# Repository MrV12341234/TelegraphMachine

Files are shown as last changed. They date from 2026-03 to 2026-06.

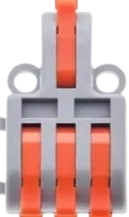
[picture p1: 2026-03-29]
imagesForSchematic/1in3out-removebg-preview.png

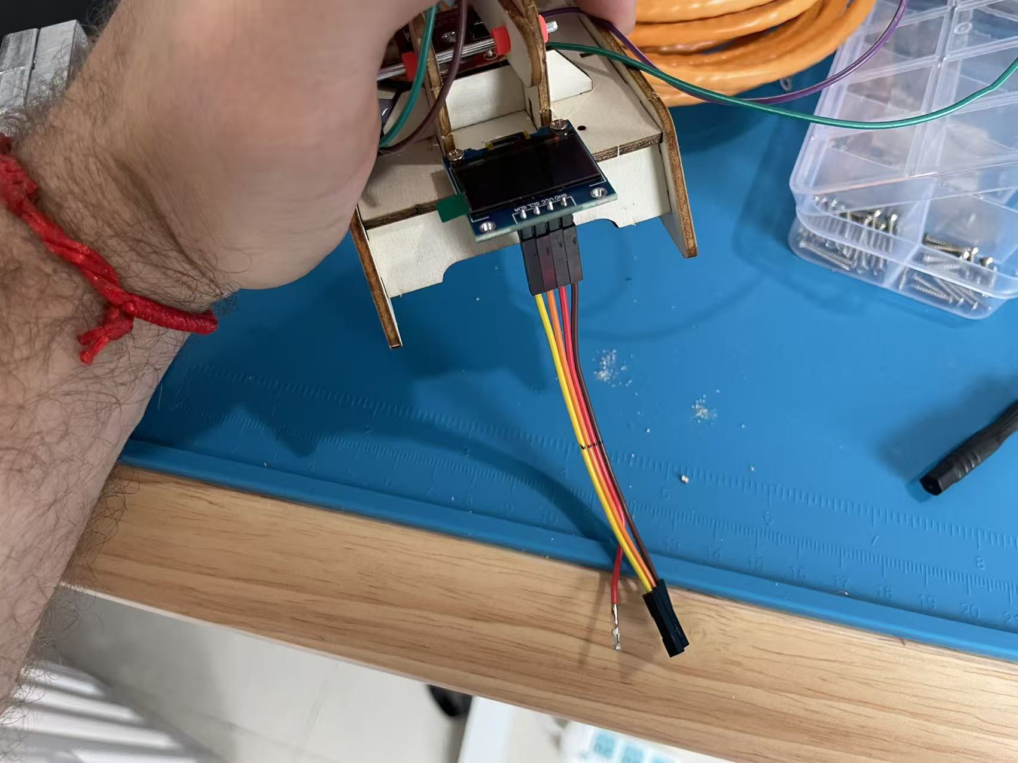
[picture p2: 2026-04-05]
imagesForSchematic/Instruction Images/ScreenWiring.jpg

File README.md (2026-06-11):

This Machine uses Telegraph DIY kits, adding an Arduino Nano and
OLED screen to send and receive telegrams.

Operation:
Either side can begin sending a message. Once one side begins, the other now must wait.
When the sender finishes (waits 7 seconds), the message will send.
The system pauses until the receiver presses their button. Then everything is reset.

Wiring:

OLED:
GND → GND
VCC → 5v board power
SDA → A4
SCK/SCL → A5

Button: one side ground, other side goes to  D2
Buzzer: One side ground, another side goes to D6

Board A D11 → Board B D10
Board B D11 → Board A D10
Board A GND → Board B GND
Board A 5V → Board B 5V
(this connection eliminates the need to power the second nano with a power source)

end of document..

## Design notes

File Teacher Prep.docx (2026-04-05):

Teacher Prep – Telegraph Machines

Materials to buy:

https://docs.google.com/spreadsheets/d/10zAsUNHxBq-jBxFfgv1lAB1i47ZYRMRfzh0iq-26aYY/edit?gid=0#gid=0

Silicon mat for each team (to pick up project and move it each day)

Long wiring from each station (4 wires each run)

2 Nano’s (one per station)

2 OLED (128x64)

2 bread boards

2 DIY telegraph kits (will not use as instructed)

Breadboard pins (both male to male and female to female

Hot glue gun

Boxes (about 10cm x10cmx5cm). No problem if its bigger.

MrV to prep for each group:

- Solder wires to button board (see photo). Use the edge colors of each groups long female to female wire jumper set. Remove the black plastic from green ground wire. Cut off ant and black/red wires from the board. UPDATE: TEACHER NEEDS TO REMOVE 2ND BUTTON AND BLUE A DIFFERENT BUTTON ON THE BOARD.

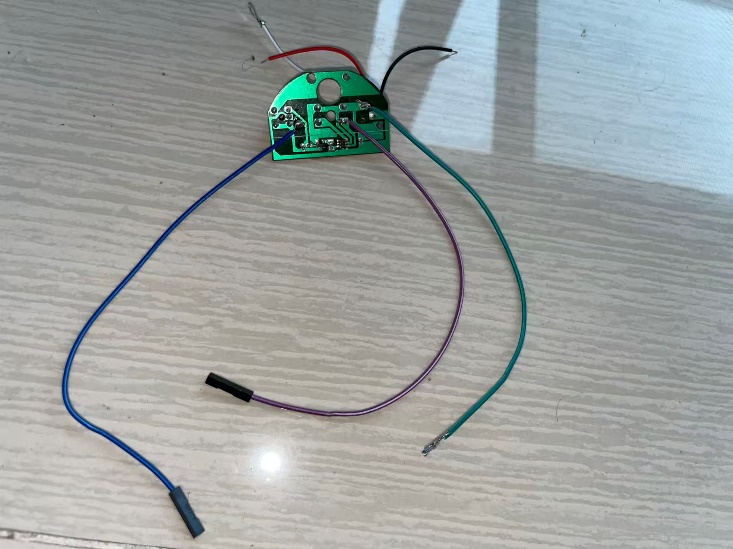
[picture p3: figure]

- Solder the ends of the ground wires for the buzzer ground and the button grounds so they more easily can go into the wire connectors
- Pre-drill box holes:
  - in top of wood box (number 20 on the step bit)
  - front (ethernet cable, 10 on step bit)
  - Side of ONE Box per group (usb, 14 on step bit)
- Create wire harness for OLED screens. Take black platic end off the VCC (5v) wire to put into the connector

Introducing the project:

Explain what a nano is (how each pin either accepts input or put output.

Explain how a machine reads code

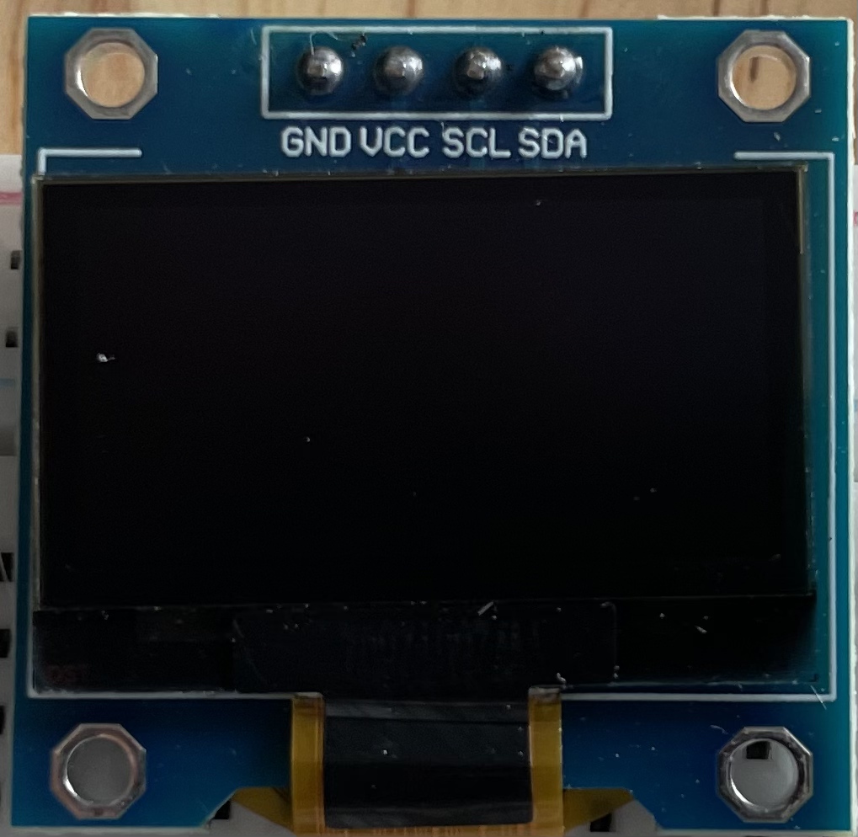
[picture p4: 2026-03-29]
imagesForSchematic/OLED.jpg

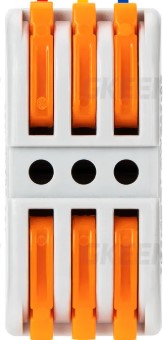
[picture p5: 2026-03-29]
imagesForSchematic/SchematicImages/3in3out.jpg

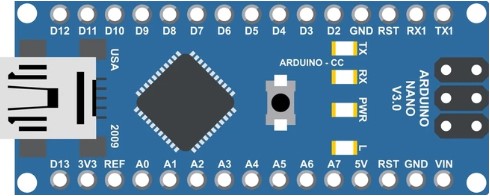
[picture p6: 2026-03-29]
imagesForSchematic/NanoCartoon.jpg

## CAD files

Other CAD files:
WiringSchematic.dwg

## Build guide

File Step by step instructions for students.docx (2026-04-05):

Step by step instructions for students

1. You will first setup the two 11cmX11cm boxes. This telegraph system has a sender and receiver box. The boxes are very similar but have slight differences in the wiring and the sender box has an additional hole for the power.
2. Drill 2cm hole in top of box

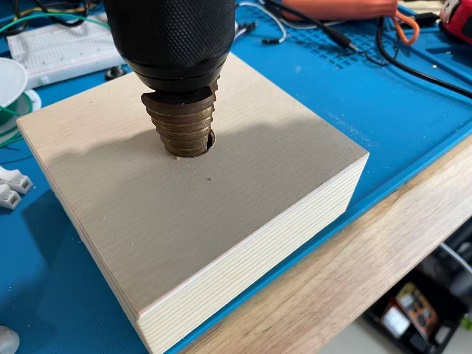
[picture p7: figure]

3. Drill 14mm hole in front of box. The “receiver” box will have only these two holes. For the “sender” box you need to drill a second 14mm hole in one of your two boxes, one box needs a usb cable).
4. Unpackage and remove the items from the Telegraph kit. These are the only parts we will use from this kit:

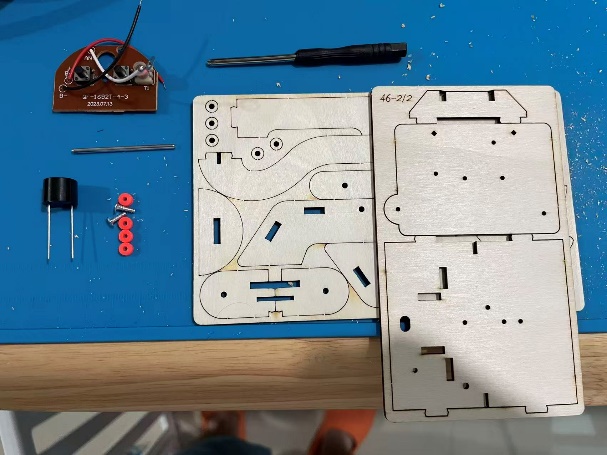
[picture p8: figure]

5. Ensure the brown button board has the wires added for this project (teacher will have previously done this).

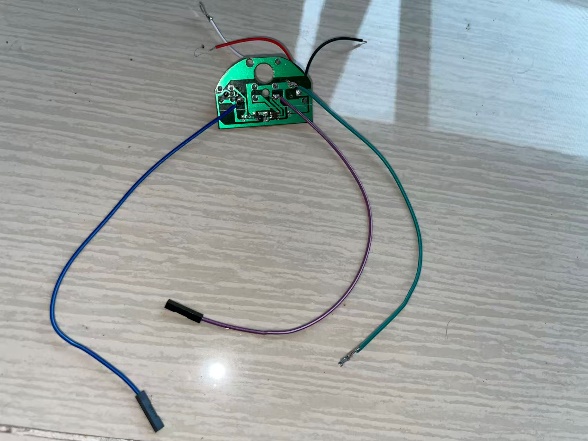
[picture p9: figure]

6. Assemble the telegraph kit with the parts shown in step three:

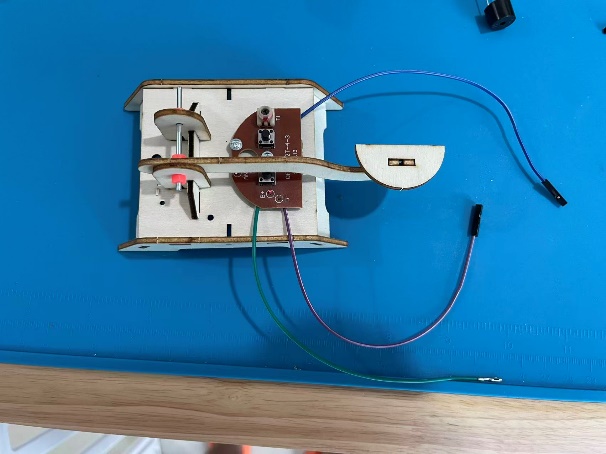
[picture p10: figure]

7. Take the black buzzer. Attach a long BROWN wire to the plus (+) terminal. Attach a GREEN wire to the other side. Remove the black plastic end from the other end of the green wire

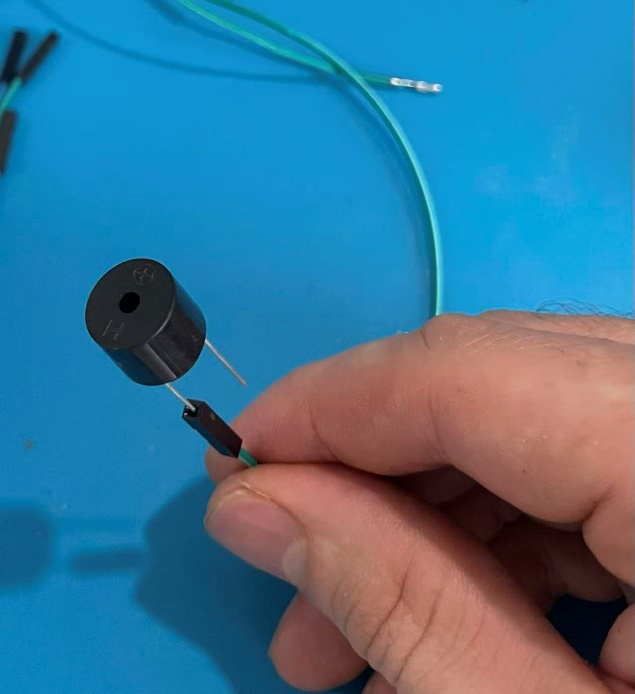
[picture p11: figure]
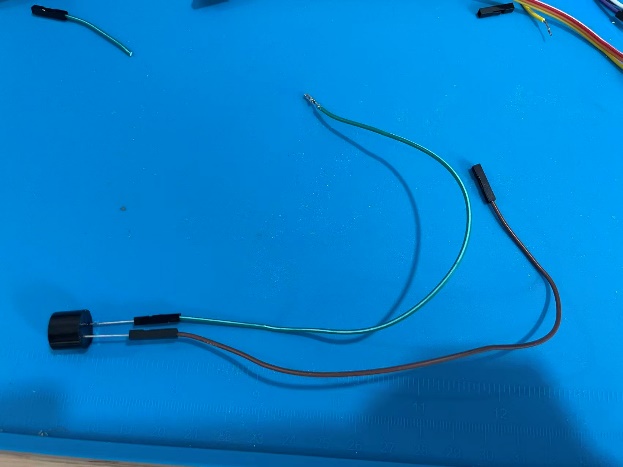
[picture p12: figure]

8. Apply hot glue to both the green and brown connection (see photo below). Ensure no glue is going between the silver posts. Then mount the buzzer somewhere on the telegraph machine using hot glue.

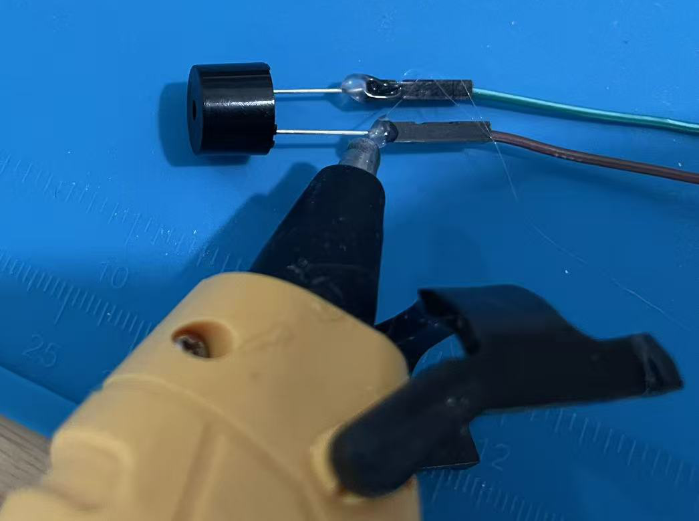
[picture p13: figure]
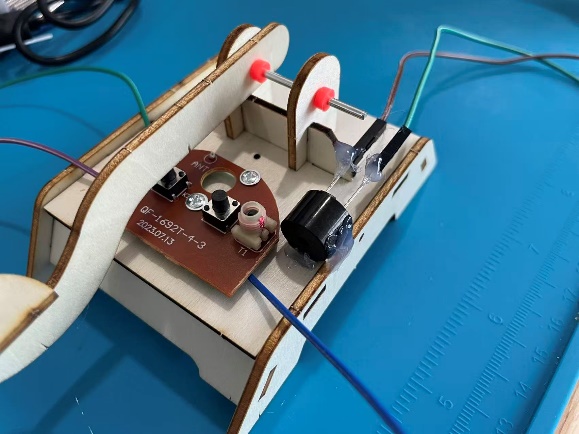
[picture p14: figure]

9. Use a pen to mark the holes of the screen. Drill one hole with a 1.5mm drill bit to drill the holes. Use 2 of the wooden spaces provided in the kit as a spacer between the screen and the base. Mount the screen with one hole then drill the second hole through the hole of the screen. Use two screws to attach (you need different screws than came in the kit).

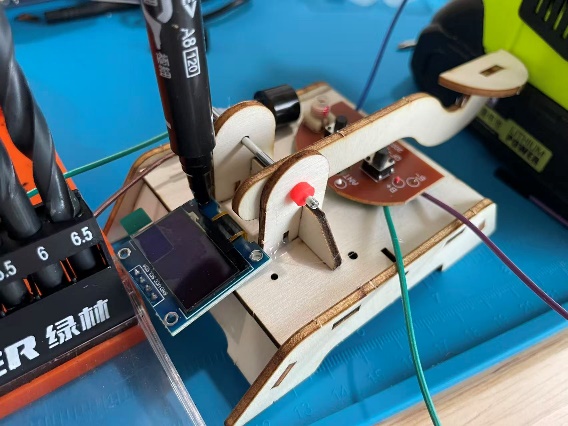
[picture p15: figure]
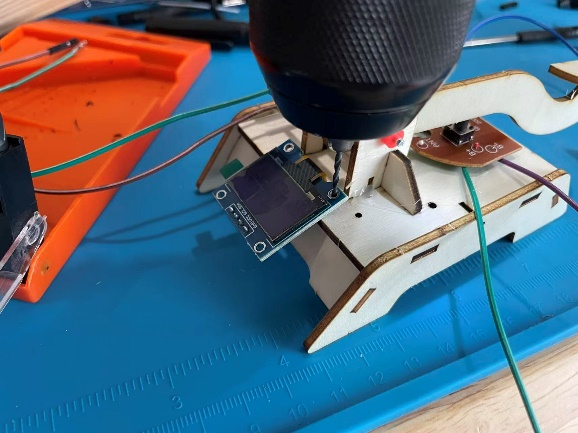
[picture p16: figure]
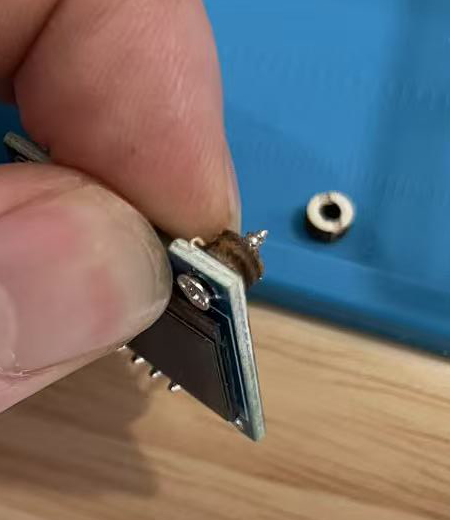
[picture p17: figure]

Alternatively, you can use a hole on the kit and mount the screen using the bottom left hole. The screen will be a little sideways, but the install is much easier:

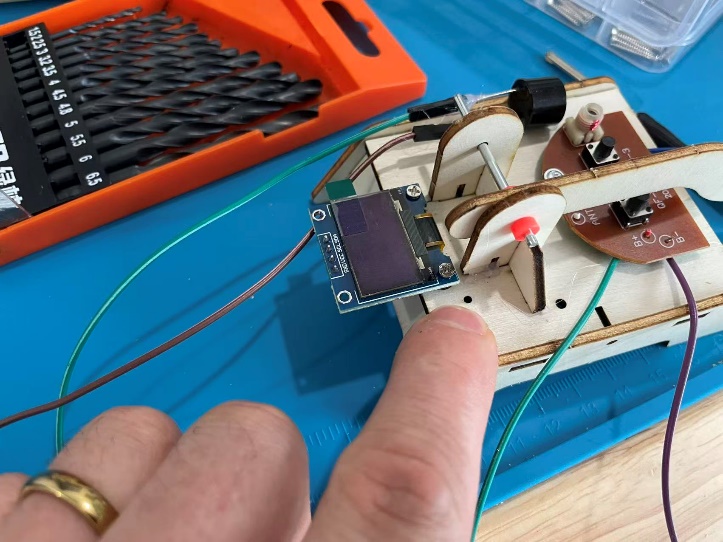
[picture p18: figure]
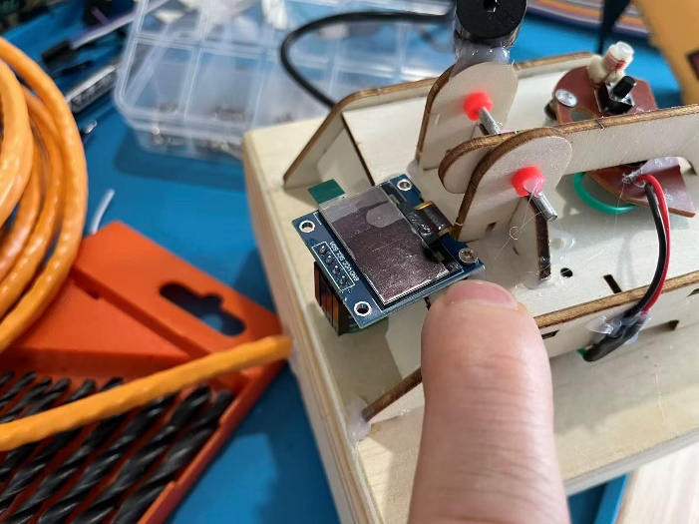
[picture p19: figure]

10. Take these four wires from your short Female-to-female wire set. Ensure the colors are like this: GND → Brown (GN )

VCC → Red (5v board power )

SCL → Orange (A5)

SDA → Yellow (A4)

Remove the black plastic end from the Red wire

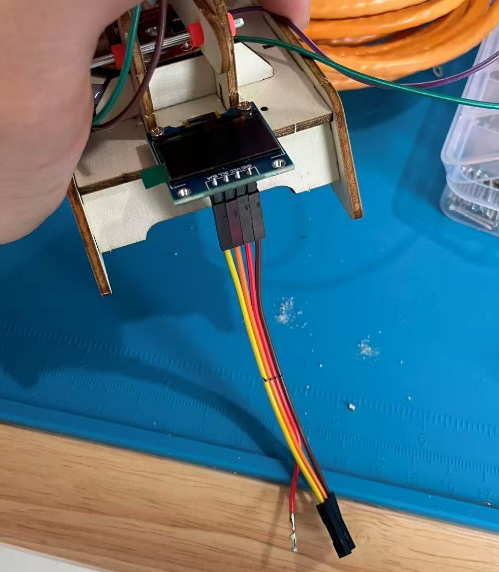
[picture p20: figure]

11. Now that the Telegraph button half is finished, insert all the wires into the large hole of your box. See the below photos to see how to route each device wires into the hole. ENSURE THE SCREEN IS FACING THE “FRONT” WHERE THE SIDE HOLE IS LOCATED. Add two small hot glue welds to secure the telegraphy machine to the box (when the project is complete we will put more glue here).

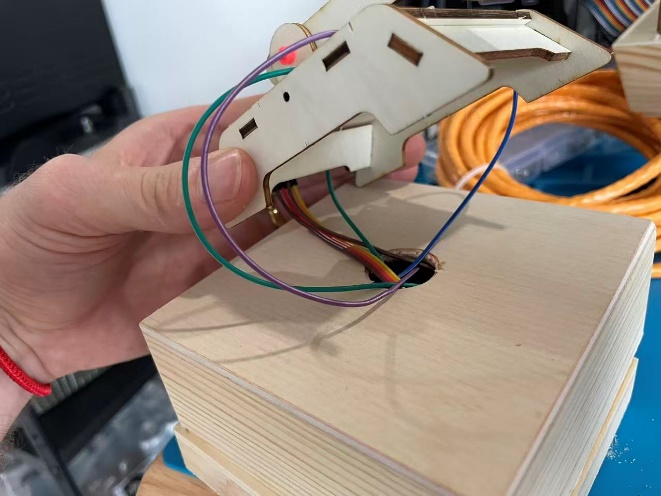
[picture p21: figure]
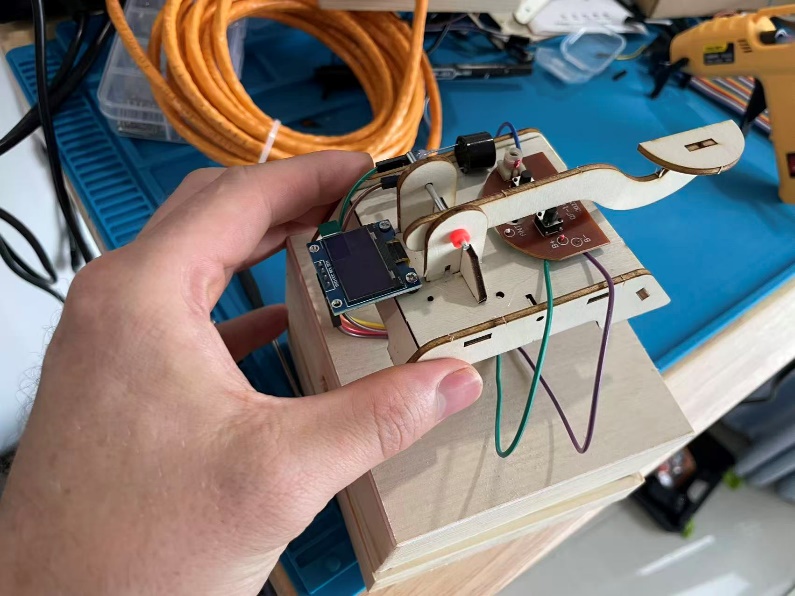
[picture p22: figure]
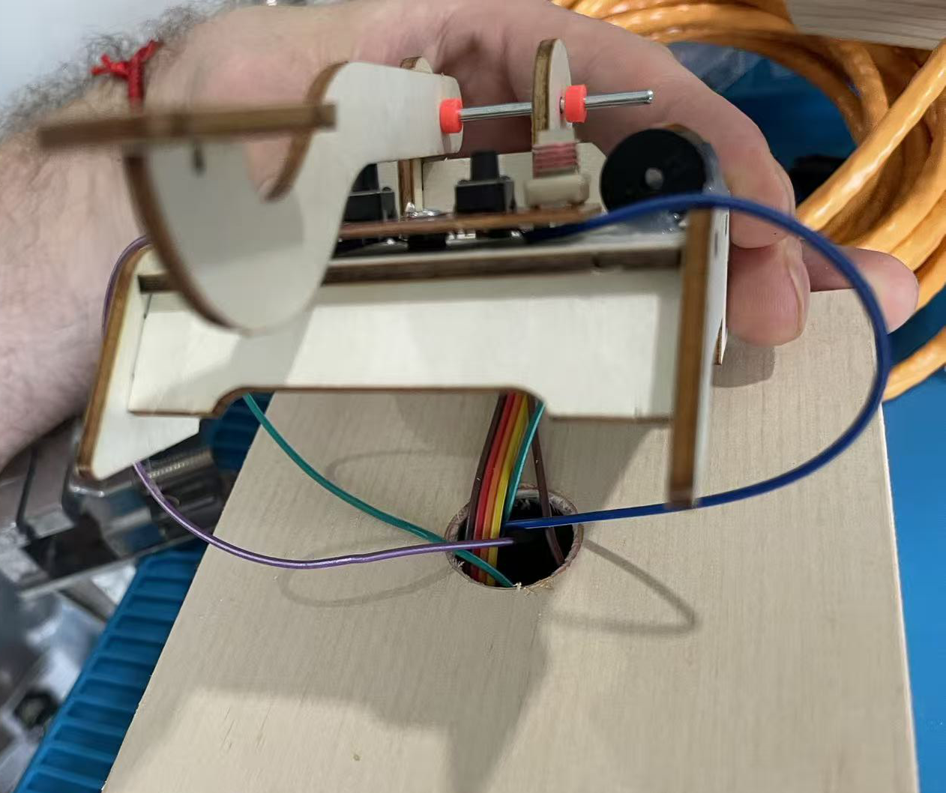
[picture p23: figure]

12. Prepare (splice) the ethernet cable so its ready to be connected. Optionally, you can install a female-to-female RJ45 (Ethernet) connector to the box to avoid a permeant connection between the two boxes. See photos below.  To prepare the ethernet cable, strip back the plastic coating about 1.5cm from the ends of each of the 8 wires inside.

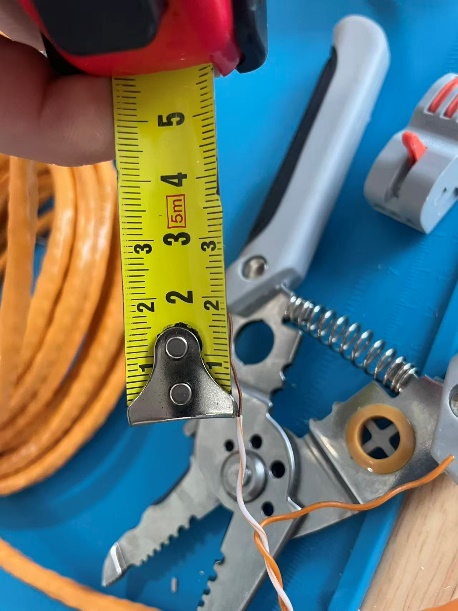
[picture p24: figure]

After stripping all the ends, twist together the bare ends of each color. Green to green, orange to orange, brown to brown, and blue to blue:

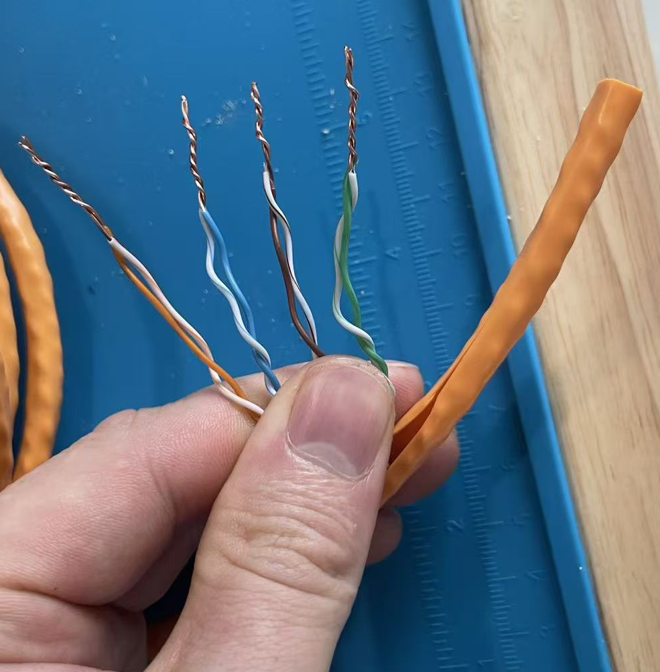
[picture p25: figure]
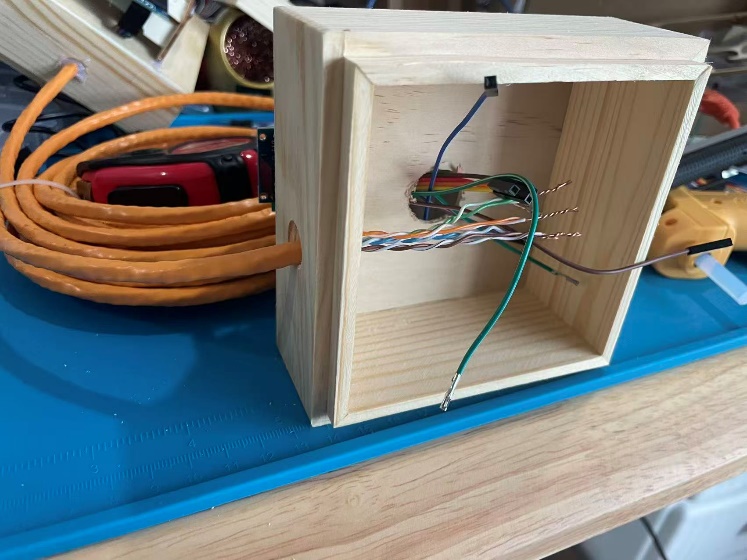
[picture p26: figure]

These are the optional RJ45 to Rj45 connectors you can use for a quick disconnect and making the boxes more portable:

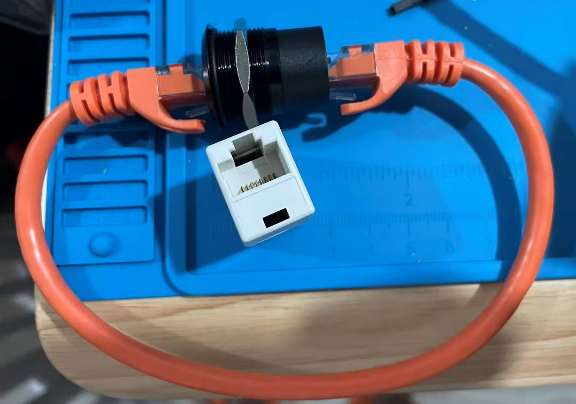
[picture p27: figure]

13. Take the black plastic off a red, green, blue, and orange wire from your short female-to-female wires:

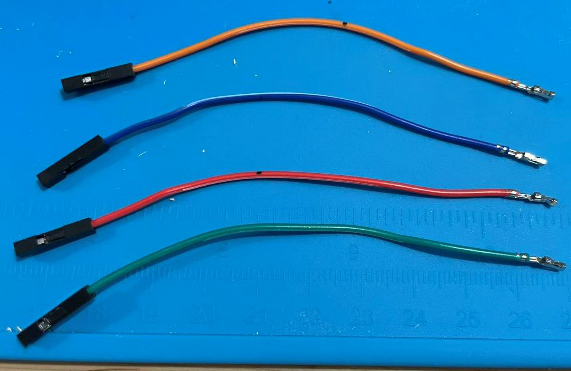
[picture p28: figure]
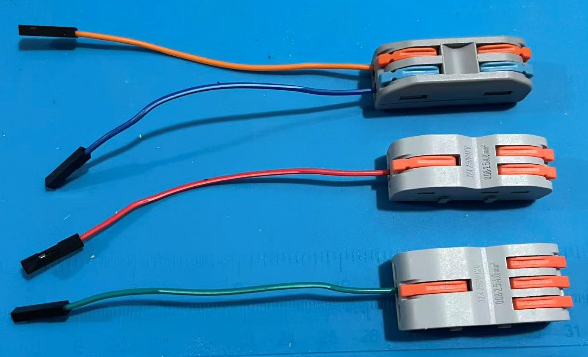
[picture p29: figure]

14. Follow the wiring schematic to hook everything up. IMPORTANT: The wiring diagram is for the sender box. The receiver box will have D10 and D11 switched. On the receiver box, D10 should have the orange wire an D11 the blue wire. Otherwise, all the grounds go into the 3-to-1 connector with the single side going to the computer. The screen goes to a 2-to-1 connector. The other side of the 2-to-1 connector goes to the opposite box same connector.

Button: one side ground, other side goes to D2

Buzzer: One side ground, another side goes to D6

15. When finished and confirmed the system is working, put a small amount of hot glue on each connection to the computer.

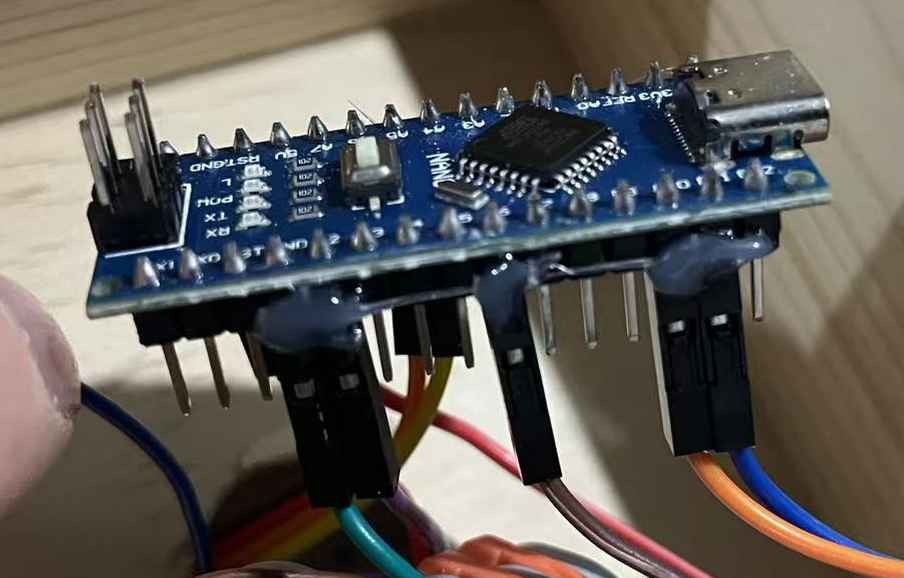
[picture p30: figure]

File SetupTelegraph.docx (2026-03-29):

Grounds together: Button, buzzer, oled, 2nd Nano

Power together: OLED, 2nd Nano

OLED

GND → GND

VCC → 5v board power

SDA → A4

SCK/SCL → A5

Button: one side ground, other side goes to D2

Buzzer: One side ground, another side goes to D6

Board A D11 → Board B D10

Board B D11 → Board A D10

Board A GND → Board B GND

Board A 5V → Board B 5V

text size 1 is great. Its small, but should allow us to display a lot of morse code, so let’s stay with this. Ive now added a button to each board (ground goes to ground and the other side of the button goes to D2.

Ive added a buzzer to each bread board, one side is ground and the other is to D6.

Ive connected the two boards together with this wiring:

Right now I have two separate bread boards, each I will setup the same and then will connect them together to act as my sending and receiving telegraph machines. Can you write me a script that I can add to each nano. I want a short press and a long press to build the letters. At the end of a word, please put a “/” on the receiving end screen to make it easy to tell the difference between words.

What was the timing arrangement for morse code and a telegraph machine for determining the end of the word? And of a sentence? Im just not sure how the coding will determine the end of a single letter, a single word, and a sentence. Any ideas? My best idea is 1 second pause for letters. 3 second pause for words. And 7 second pause for end of message.

I need the script to determine how a message is incoming and when a message is incoming, that machine cant push the button (send message).

we should have both machines start with a message that says “press the button to begin sending a message”.

Then if one machine starts pressing the button, the other machine shows a small message at the top that says something like “Incoming message” and removes the “press the button to begin”

And while the sending board is typing their message, lets display their dots and dashes. And then display the dots and dashes on the receiving machine when each word is finished from the sender (keeping the “incoming message” line at the top of the screen). So each word the receiver sends, it is then sent, only showing dots and dashes on both machines.

When the sender is done (waits 7 seconds), a message is shown on the senders screen saying “message sent. Receiver will clear message when theyre finished”.

Now the receiving machine will have the complete message. They will see all the dots and dashes. Im hoping the message can be stored and I have a 3 second message appear on the oled screen that says “Message receiving finished, press button to clear” and then that message disappears and the dots and dashes from the message appears again.

Im hoping all of this wont be to much coding for a Nano to store.

Also, would it be possible to power board b with power from board a? this way during my school event, I would only need power at the one end. Im sure I can run a 5v from nano A over to the vin of nano B, but im not sure if this is acceptable. If this is not a danger and acceptable, just lmk and I can wire it up (tell me exactly how you want me to wire it to match your script).

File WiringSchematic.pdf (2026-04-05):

5v on Telegraph B (Brown Wire in Ethernet cable) Ground on Telegraph B (Green Wire in Ethernet cable) D11 on Telegraph B D10 on Telegraph B

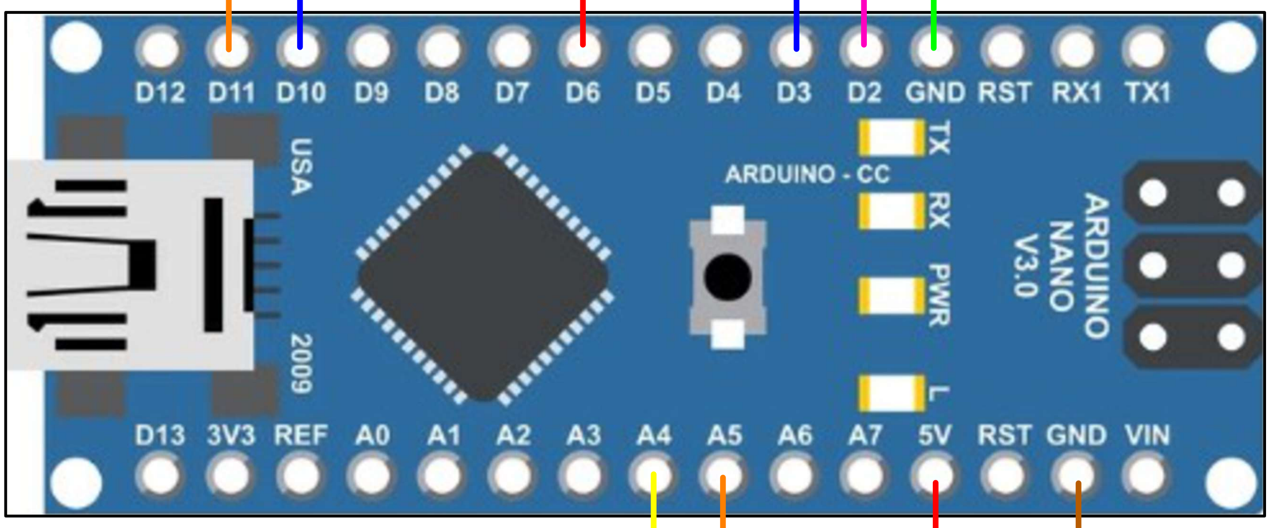
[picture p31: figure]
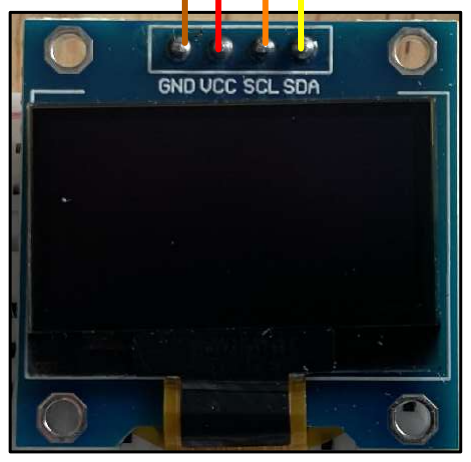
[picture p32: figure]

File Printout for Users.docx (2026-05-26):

Morse Code

1. Pick your letters and first write your code on paper. Type the dots and dashes quickly, then wait 2 seconds to start the next letter. Between each word is a “/” (wait 3 seconds and a “/” will appear).

Example:

…. . .-.. .-.. ---- / … -.- -.--

H E L L O S K Y

2. Using the machine:

Quick press for dot

Long press for dash

- Letters: Quickly press the dots and dashes when you start. After you complete a letter, wait two seconds to finalize your letter, then begin typing your next sequence of dots and dashes.
- Words: At the end of a word, wait 3 seconds, you will see a “/” appear
- End of message: Wait 7 seconds and the message will send.
- Letters: 2 second pause
- Words: 3 second pause. (“/” appears)
- End of message: 7 Second pause

Operation:

Either side can begin sending a message. Once one side begins, the other now must wait. When the sender finishes (waits 7 seconds), the message will send. The system pauses until the receiver presses their button. Then everything is reset. There is a cancel button on the right if you mess up typing your message

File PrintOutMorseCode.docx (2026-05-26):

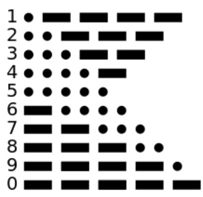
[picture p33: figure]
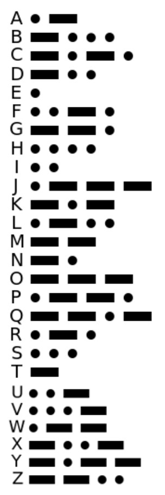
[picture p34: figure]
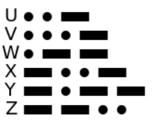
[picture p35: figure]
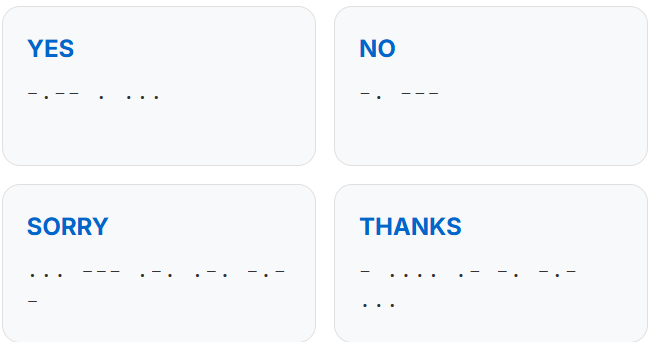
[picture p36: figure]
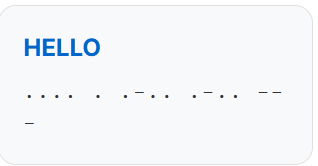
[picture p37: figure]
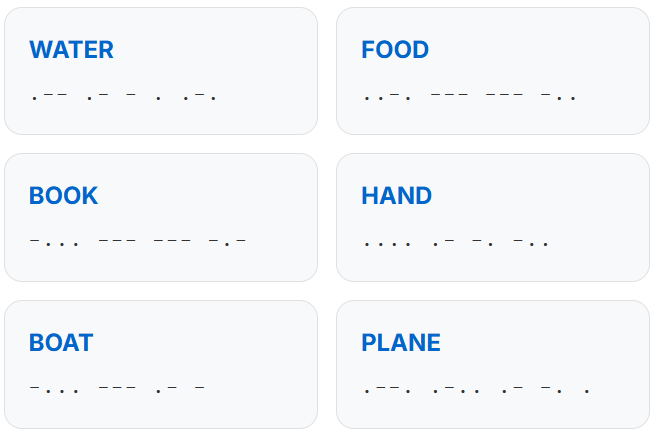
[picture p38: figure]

Morse Code

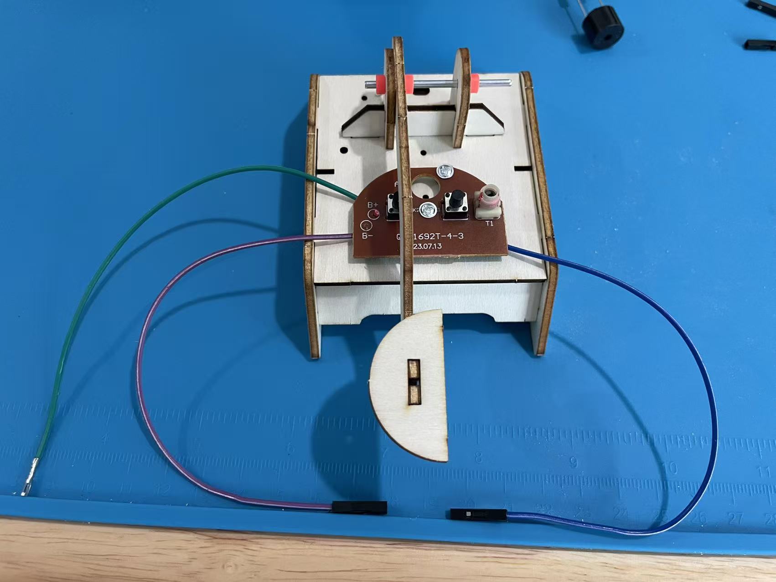
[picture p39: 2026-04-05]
imagesForSchematic/Instruction Images/TelegraphKitAssembled1.jpg

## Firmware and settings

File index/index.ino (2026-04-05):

#include <Wire.h>
#include <Adafruit_GFX.h>
#include <Adafruit_SSD1306.h>
#include <SoftwareSerial.h>
#include <string.h>

#define SCREEN_WIDTH 128
#define SCREEN_HEIGHT 64
#define OLED_ADDR 0x3C

// ---------------- Pins ----------------
const int BUTTON_PIN = 2;         // send button
const int CANCEL_BUTTON_PIN = 3;  // cancel current send
const int BUZZER_PIN = 6;

// Board A D11 -> Board B D10
// Board B D11 -> Board A D10
const int LINK_RX_PIN = 10;
const int LINK_TX_PIN = 11;

// ---------------- Timing ----------------
const unsigned long DEBOUNCE_MS           = 25;
const unsigned long MIN_PRESS_MS          = 40;
const unsigned long DOT_DASH_THRESHOLD_MS = 250;

const unsigned long LETTER_GAP_MS   = 1000; // end of letter
const unsigned long WORD_GAP_MS     = 3000; // end of word
const unsigned long MESSAGE_END_MS  = 7000; // end of full message

const unsigned long OVERLAY_MS      = 3000;
const unsigned long RENDER_MS       = 100;

// ---------------- Morse storage ----------------
const int MESSAGE_MAX = 110;  // full committed message shown on screen
const int WORD_MAX    = 48;   // current word (hidden on receiver until complete)
const int LETTER_MAX  = 8;    // current letter in Morse

// ---------------- Buzzer ----------------
const int BEEP_FREQ = 1200;
const unsigned long DOT_BEEP_MS  = 90;
const unsigned long DASH_BEEP_MS = 220;

// ---------------- Objects ----------------
Adafruit_SSD1306 display(SCREEN_WIDTH, SCREEN_HEIGHT, &Wire, -1);
SoftwareSerial linkSerial(LINK_RX_PIN, LINK_TX_PIN); // RX, TX

// ---------------- State ----------------
enum Mode {
  MODE_IDLE,
  MODE_SENDING,
  MODE_RECEIVING,
  MODE_RX_DONE,
  MODE_WAIT_CLEAR
};

enum OverlayType {
  OVERLAY_NONE,
  OVERLAY_SENT,
  OVERLAY_RX_FINISHED,
  OVERLAY_CANCELED
};

Mode mode = MODE_IDLE;
OverlayType overlayType = OVERLAY_NONE;
unsigned long overlayUntil = 0;

char messageBuffer[MESSAGE_MAX + 1]; // completed visible message
char currentWord[WORD_MAX + 1];      // current word
char currentLetter[LETTER_MAX + 1];  // current letter

bool lastRawButton = HIGH;
bool stableButton = HIGH;
unsigned long lastDebounceTime = 0;
unsigned long pressStartTime = 0;

bool lastRawCancelButton = HIGH;
bool stableCancelButton = HIGH;
unsigned long lastCancelDebounceTime = 0;

unsigned long lastSymbolReleaseTime = 0;
bool hasMessageContent = false;
bool startTokenSent = false;
bool letterGapCommitted = false;
bool wordGapCommitted = false;

unsigned long lastRenderTime = 0;

// ---------------- Utility ----------------
void clearBuffers() {
  messageBuffer[0] = '\0';
  currentWord[0] = '\0';
  currentLetter[0] = '\0';
}

void clearSessionFlags() {
  hasMessageContent = false;
  startTokenSent = false;
  letterGapCommitted = false;
  wordGapCommitted = false;
  lastSymbolReleaseTime = 0;
}

bool overlayActive() {
  return millis() < overlayUntil;
}

void showOverlay(OverlayType t) {
  overlayType = t;
  overlayUntil = millis() + OVERLAY_MS;
}

void clearOverlay() {
  overlayType = OVERLAY_NONE;
  overlayUntil = 0;
}

void appendCharSafe(char* dest, int maxLen, char c) {
  int len = strlen(dest);
  if (len < maxLen) {
    dest[len] = c;
    dest[len + 1] = '\0';
  }
}

void appendTextSafe(char* dest, int maxLen, const char* src) {
  int len = strlen(dest);
  while (*src && len < maxLen) {
    dest[len++] = *src++;
  }
  dest[len] = '\0';
}

void beepForSymbol(char symbol) {
  if (symbol == '.') {
    tone(BUZZER_PIN, BEEP_FREQ, DOT_BEEP_MS);
  } else if (symbol == '-') {
    tone(BUZZER_PIN, BEEP_FREQ, DASH_BEEP_MS);
  }
}

void sendToken(char c) {
  linkSerial.write(c);
}

void forceIdleState() {
  clearBuffers();
  clearOverlay();
  clearSessionFlags();
  mode = MODE_IDLE;
}

// ---------------- Buffer builders ----------------
void finalizeCurrentLetterToWord() {
  if (currentLetter[0] == '\0') return;
  appendTextSafe(currentWord, WORD_MAX, currentLetter);
  appendCharSafe(currentWord, WORD_MAX, ' ');
  currentLetter[0] = '\0';
}

void appendCurrentWordToMessageWithSlash() {
  if (currentWord[0] == '\0') return;
  appendTextSafe(messageBuffer, MESSAGE_MAX, currentWord);
  appendTextSafe(messageBuffer, MESSAGE_MAX, "/ ");
  currentWord[0] = '\0';
}

void appendCurrentWordToMessageNoSlash() {
  if (currentWord[0] == '\0') return;
  appendTextSafe(messageBuffer, MESSAGE_MAX, currentWord);
  currentWord[0] = '\0';
}

// ---------------- Session control ----------------
void startSendingSession() {
  clearBuffers();
  clearOverlay();

  mode = MODE_SENDING;
  clearSessionFlags();
}

void finishSendingSession() {
  // Flush pending letter/word before ending
  if (currentLetter[0] != '\0') {
    finalizeCurrentLetterToWord();
    sendToken(' ');   // end letter
  }

  if (currentWord[0] != '\0') {
    appendCurrentWordToMessageNoSlash();
    sendToken('>');   // final word, no slash
  }

  sendToken('|');     // end of message

  mode = MODE_WAIT_CLEAR;
  showOverlay(OVERLAY_SENT);

  clearBuffers();
  clearSessionFlags();
}

void startReceivingSession() {
  clearBuffers();
  clearOverlay();
  clearSessionFlags();
  mode = MODE_RECEIVING;
}

void finishReceivingSession() {
  if (currentLetter[0] != '\0') {
    finalizeCurrentLetterToWord();
  }
  if (currentWord[0] != '\0') {
    appendCurrentWordToMessageNoSlash();
  }

  mode = MODE_RX_DONE;
  showOverlay(OVERLAY_RX_FINISHED);
}

void clearReceivedMessage() {
  sendToken('C');   // tell sender it may return to idle
  forceIdleState();
}

void cancelSendingSession() {
  if (mode != MODE_SENDING) return;

  // Only notify the other box if this message had already started
  if (startTokenSent) {
    sendToken('X');   // cancel token
  }

  forceIdleState();
  showOverlay(OVERLAY_CANCELED);
}

// ---------------- Incoming serial ----------------
// Tokens:
// 'S' = start message
// '.' '-' = Morse symbols
// ' ' = end of letter
// '/' = end of word
// '>' = flush final word without slash
// '|' = end of message
// 'C' = receiver cleared message
// 'X' = sender canceled current message
void handleIncomingToken(char token) {
  if (token == 'X') {
    // Sender canceled current message. Both sides return to idle.
    forceIdleState();
    showOverlay(OVERLAY_CANCELED);
    return;
  }

  if (token == 'C') {
    if (mode == MODE_WAIT_CLEAR) {
      forceIdleState();
    }
    return;
  }

  if (token == 'S') {
    if (mode == MODE_IDLE) {
      startReceivingSession();
    }
    return;
  }

  if (mode != MODE_RECEIVING) return;

  if (token == '.' || token == '-') {
    appendCharSafe(currentLetter, LETTER_MAX, token);
    beepForSymbol(token);
    return;
  }

  if (token == ' ') {
    finalizeCurrentLetterToWord();
    return;
  }

  if (token == '/') {
    finalizeCurrentLetterToWord();
    appendCurrentWordToMessageWithSlash();
    return;
  }

  if (token == '>') {
    finalizeCurrentLetterToWord();
    appendCurrentWordToMessageNoSlash();
    return;
  }

  if (token == '|') {
    finishReceivingSession();
    return;
  }
}

void processIncomingSerial() {
  while (linkSerial.available()) {
    char c = (char)linkSerial.read();
    handleIncomingToken(c);
  }
}

// ---------------- Button handling ----------------
void processCancelButton() {
  bool raw = digitalRead(CANCEL_BUTTON_PIN);

  if (raw != lastRawCancelButton) {
    lastCancelDebounceTime = millis();
    lastRawCancelButton = raw;
  }

  if ((millis() - lastCancelDebounceTime) <= DEBOUNCE_MS) return;

  if (raw != stableCancelButton) {
    stableCancelButton = raw;

    // Button pressed
    if (stableCancelButton == LOW) {
      if (mode == MODE_SENDING) {
        cancelSendingSession();
      }
    }
  }
}

void processButton() {
  bool raw = digitalRead(BUTTON_PIN);

  if (raw != lastRawButton) {
    lastDebounceTime = millis();
    lastRawButton = raw;
  }

  if ((millis() - lastDebounceTime) <= DEBOUNCE_MS) return;

  if (raw != stableButton) {
    stableButton = raw;

    // Button pressed
    if (stableButton == LOW) {
      if (overlayActive()) return;

      if (mode == MODE_RX_DONE) {
        clearReceivedMessage();
        return;
      }

      if (mode == MODE_RECEIVING || mode == MODE_WAIT_CLEAR) {
        return; // locked during incoming message or waiting for receiver clear
      }

      if (mode == MODE_IDLE) {
        startSendingSession();
      }

      if (mode == MODE_SENDING) {
        pressStartTime = millis();
      }
    }
    // Button released
    else {
      if (mode != MODE_SENDING) return;

      unsigned long pressDuration = millis() - pressStartTime;
      if (pressDuration < MIN_PRESS_MS) return;

      char symbol = (pressDuration < DOT_DASH_THRESHOLD_MS) ? '.' : '-';

      if (!startTokenSent) {
        sendToken('S');
        startTokenSent = true;
      }

      appendCharSafe(currentLetter, LETTER_MAX, symbol);
      sendToken(symbol);
      beepForSymbol(symbol);

      hasMessageContent = true;
      lastSymbolReleaseTime = millis();
      letterGapCommitted = false;
      wordGapCommitted = false;
    }
  }
}

// ---------------- Gap timing ----------------
void processSendingGapTimers() {
  if (mode != MODE_SENDING) return;
  if (stableButton == LOW) return; // still holding button
  if (!hasMessageContent) return;

  unsigned long gap = millis() - lastSymbolReleaseTime;

  if (!letterGapCommitted && currentLetter[0] != '\0' && gap >= LETTER_GAP_MS) {
    finalizeCurrentLetterToWord();
    sendToken(' ');
    letterGapCommitted = true;
  }

  if (!wordGapCommitted && currentWord[0] != '\0' && gap >= WORD_GAP_MS) {
    appendCurrentWordToMessageWithSlash();
    sendToken('/');
    wordGapCommitted = true;
  }

  if (gap >= MESSAGE_END_MS) {
    finishSendingSession();
  }
}

// ---------------- Display rendering ----------------
int bodyRow = 1;
int bodyCol = 0;

void beginBodyText() {
  bodyRow = 1;
  bodyCol = 0;
}

void drawBodyChar(char c) {
  if (bodyRow > 7) return;

  display.setCursor(bodyCol * 6, bodyRow * 8);
  display.write(c);

  bodyCol++;
  if (bodyCol >= 21) {
    bodyCol = 0;
    bodyRow++;
  }
}

void drawBodyText(const char* text) {
  for (int i = 0; text[i] != '\0'; i++) {
    drawBodyChar(text[i]);
  }
}

void drawOverlay() {
  display.clearDisplay();
  display.setTextSize(1);
  display.setTextColor(SSD1306_WHITE);

  if (overlayType == OVERLAY_SENT) {
    display.setCursor(0, 8);
    display.println(F("Message sent"));
    display.setCursor(0, 24);
    display.println(F("Receiver clears it"));
  } else if (overlayType == OVERLAY_RX_FINISHED) {
    display.setCursor(0, 8);
    display.println(F("Message finished"));
    display.setCursor(0, 24);
    display.println(F("Press down to clear"));
  } else if (overlayType == OVERLAY_CANCELED) {
    display.setCursor(0, 8);
    display.println(F("Message canceled..."));
    display.setCursor(0, 24);
    display.println(F("Going back home"));
  }

  display.display();
}

void renderDisplay() {
  if (millis() - lastRenderTime < RENDER_MS) return;
  lastRenderTime = millis();

  if (overlayActive()) {
    drawOverlay();
    return;
  }

  display.clearDisplay();
  display.setTextSize(1);
  display.setTextColor(SSD1306_WHITE);

  display.setCursor(0, 0);
  if (mode == MODE_IDLE) {
    display.println(F("Press down to start a message"));
  } else if (mode == MODE_SENDING) {
    display.println(F("Type your message"));
  } else if (mode == MODE_RECEIVING) {
    display.println(F("Incoming message:"));
  } else if (mode == MODE_RX_DONE) {
    display.println(F("Press down to clear"));
  } else if (mode == MODE_WAIT_CLEAR) {
    display.println(F("Message Sent..."));
  }

  beginBodyText();

  if (mode == MODE_SENDING) {
    drawBodyText(messageBuffer);
    drawBodyText(currentWord);
    drawBodyText(currentLetter);
  } else if (mode == MODE_RECEIVING || mode == MODE_RX_DONE) {
    drawBodyText(messageBuffer); // receiver only shows completed words
  } else if (mode == MODE_WAIT_CLEAR) {
    drawBodyText("Receiver is decoding.");
    bodyRow += 2;   // skip one blank line
    bodyCol = 0;
    drawBodyText("They will clear");
    bodyRow += 1;   // goto next line
    bodyCol = 0;
    drawBodyText("messages when");
    bodyRow += 1;   // goto next line
    bodyCol = 0;
    drawBodyText("finished");
  }

  display.display();
}

// ---------------- Setup / Loop ----------------
void setup() {
  pinMode(BUTTON_PIN, INPUT_PULLUP);
  pinMode(CANCEL_BUTTON_PIN, INPUT_PULLUP);
  pinMode(BUZZER_PIN, OUTPUT);

  Wire.begin();
  linkSerial.begin(9600);

  if (!display.begin(SSD1306_SWITCHCAPVCC, OLED_ADDR)) {
    while (true) {}
  }

  clearBuffers();
  clearOverlay();
  clearSessionFlags();

  display.clearDisplay();
  display.setTextSize(1);
  display.setTextColor(SSD1306_WHITE);
  display.setCursor(0, 0);
  display.println(F("Press down to send"));
  display.display();
}

void loop() {
  processIncomingSerial();
  processCancelButton();
  processButton();
  processSendingGapTimers();
  renderDisplay();
}

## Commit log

2026-03-29 Initial Upload
    [WiringSchematic.dwg]
2026-03-29 Wiring Update
    cleaned up lines, no major changes
    [WiringSchematic.dwg]
2026-04-05 Updated instructions
    [WiringSchematic.dwg]
